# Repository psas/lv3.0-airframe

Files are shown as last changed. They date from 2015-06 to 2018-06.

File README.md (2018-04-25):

# PSAS Launch Vehicle 3 (LV3) 🚀

This is the repo for the LV3 airframe. This holds everything you need to know about making a rocket out of carbon fiber. This includes CAD files, design and prototyping logs, simulation and testing data, most of all the manufacturing procedures for the carbon fiber airframe modules.  

If you aren't allowed to push, send Joe or Andrew your Github username and ask for access. (This is different from getting added to the PSAS "organization".)

If you're looking to copy or build on this work check out the [doc directory](/doc/), especially the [layup procedure](/doc/mfg/moduleProcedure.md) and please message the people who have committed frequently/recently with any questions (or better yet, [make an issue with your question](https://github.com/psas/lv3.0-airframe/issues)).

If you want some quick physical specifications on the airframe, checkout the [quick facts.](doc/quickFacts.md)
For more detailed info, we have a [model](sim/ORK/LV3_L13.ork) for [OpenRocket](http://openrocket.info/) and a [model](cad/LV3.SLDASM) for [SolidWorks](http://www.solidworks.com/).

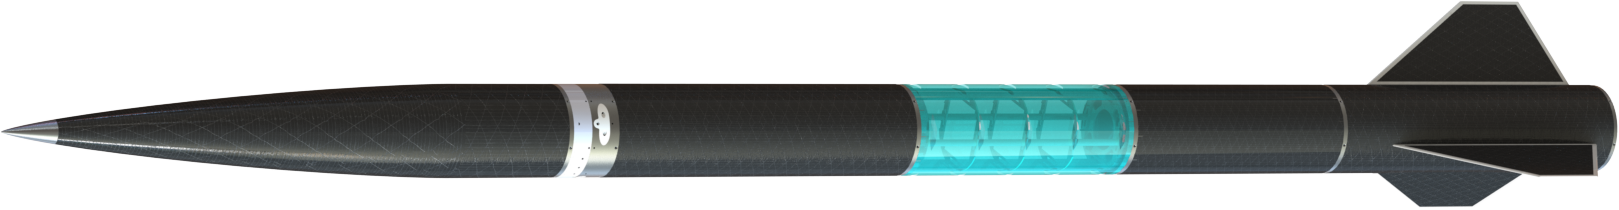
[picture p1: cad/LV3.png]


## Relevant Repositories
If you want to work on the CAD model, you'll need to have the dependencies cloned to the same directory as this repo. So, something like 

```
PSAS
├── lv3.0-airframe
├── lv3.0-recovery
├── lv3.0-camera-ring
├── lv3.0-umbilical-ring
├── sw-cad-airframe-nsr
└── reaction-control
```

You should also read the [Intro to Git workshop slides](https://drive.google.com/open?id=1pykfwvAw5q1oXGM8aLyhXPHOKDCI61YhK5w33QwzuFw) if you're new to Git
Also, read the [OreSat contributions guide](https://github.com/oresat/oresat-structure/blob/master/.github/CONTRIBUTING.md) if you're new to using SolidWorks with Git.

### Dependencies
* [psas/lv3.0-recovery](https://github.com/psas/lv3.0-recovery) -- CAD and analysis for the eNSR-based recovery system
* [psas/lv3.0-camera-ring](https://github.com/psas/lv3.0-camera-ring) -- 360 degree camera module based on the RunCam Split 2
* [psas/lv3.0-umbilical-ring](https://github.com/psas/lv3.0-umbilical-ring) -- passthrough module for the umbilical and arming switches (uses same format as camera ring)
* [psas/sw-cad-airframe-nsr](https://github.com/psas/sw-cad-airframe-nsr) -- Mechanical separation system for the nosecone/parachute
* [psas/reaction-control](https://github.com/psas/reaction-control) -- Cold gas reaction control system

### Historical
* [psas/LV3-design](https://github.com/psas/LV3-design) -- Early conceptual design of LV3
* [~~psas/mme-capstone~~](https://github.com/psas/mme-capstone) (**DEPRECATED**) -- One of the repositories created durring the 2014 capstone. This contains code for some of the tools they used. 
* [~~psas/sw-cad-carbon-fiber-process~~](https://github.com/psas/sw-cad-carbon-fiber-process) (**DEPRECATED**) -- Yet another repo from the 2014 team. This contains CAD for some of the tools they made.

## TODO:
[Check out the issues list if you're looking for something to do.](https://github.com/psas/lv3.0-airframe/issues) 
Keeping a TODO in the README never works out.

## Project Members
If you're working on the project in any way, please add yourself to this list.

IRL Name                       | Github username        | Current Role
------------------------------ | ---------------------- | ------------
Joe "Rocket Czar" Shields      | @Joedang               | project coordination; MFG; design
Leslie Elwood                  | @lelwood               | MFG; design; logistics
Alex "the Pretty Good" Farias  | @alexkazam             | MFG
Ian Zabel                      | @IanZabel              | cradle design; modelling
Kyle Blakeman                  | @kablakeman            | module sanding
Peter McCloud                  | @petermccloud          | CNC machining
Jorden Rolland                 | @JSRoland              | 
Katia                          | @kp07                  | 
Marie "Marie House" House      | @hmarie2               | anti-lithobreaking precautions
Adam Harris                    | @SaturnVF1             | MFG; manual machining
Josh Carlson                   | @paperman5             | CNC machining; design
Jacob Tiller                   | @JacobTiller           | machining; design
Erin Schmidt                   | @7deeptide             | system integration; design
Nathan Bergey                  | @natronics             | patron saint
Andrew Greenberg               | @andrewgreenberg       | benevolent dictator; pixie wrangler

## What and where
```
|-- cad						holds the Solidworks files for all the machined parts
│   ├── COTS					models for Commercial Off-The-Shelf parts
│   ├── CubeSatAirframeMount			"Cradle" that holds the flight computer (OreSat) inside LV3
|   |-- finCan
|	|-- LongFinFiles			current fin design (flyable and manufacturable)
|   |-- module					files for 18 and 24 inch modules
│   │   ├── jigs				jig for drilling side holes in module rings (and other radial parts)
│   │   └── layup
|   |-- nose					nosecone and mold subassemblies
|   |-- radome					radio-transparent fiberglass module
|   `-- railSled				part for interfacing with the launch rail
│       ├── CAM					G code for the rail sled (obsolete)
│       │   ├── Base
│       │   ├── Neck
│       │   └── Trunk
│       └── Old rail sled designs
|-- doc						all pure documentation
|   |-- aiaa-3.6.1				LaTeX template for AIAA
|   |-- extAbstract				extened abstract for the AIAA paper
|   |-- img					image resources for documentation
|   |-- mfg					step-by-step instructions for manufacturing
|   |-- paper					the conference paper we're submitting to AIAA Space
│   ├── FlightComputerMount			stuff about the Cradle
│   ├── textbook				summary of composite techniques in general
|   `-- updates					bi-monthlyish status updates on the project
|-- sim						simulations and calculations
|   |-- DATCOM					DATCOM cases for cross-validating the design (abandoned)
|   |   |-- case
|   |   |   |-- LV3				case for the LV3 airframe (not complete)
|   |   |   `-- exMiG
|   |   |-- doc					DATCOM documentation
|   |   `-- exlinux				example DATCOM cases
|   |-- ORK					open rocket models
|   |   `-- prev
|   |-- OpenFOAM				CFD models
|   |   `-- LV3\_LD-Haack			model of the 1:5 nose cone
|   |       `-- rcf_100				100-node-long mesh
|   |           |-- 0				initial conditions
|   |           |-- constant			fluid properites
|   |           `-- system			simulation parameters
|   |-- plots					plots of the open rocket data
|   |-- reductions				reductions of the openrocket simulations
|   `-- simData					output of the openrocket simulations
|-- test					data from physical tests on modules
|   `-- profilometer				surface roughness data
│   └── tinyMold				
└── tools					sources/CAD/docs for physical tools used to make LV3
    ├── Composite_Table				the table we do all the layups on
    ├── crusher-control				controller software for one of the crush testers at PSU	
    ├── oven-controller				the temperature controller for the oven
    │   ├── Oven_Controller			the temperature controller for... wait
    │   │   ├── Box				enclosure for the oven controller
    │   │   ├── OvenControl			the temperature contr-- again?!
    │   │   └── oven-controller-master		"A Deja Vu is usually a glitch in the Matrix."
    │   └── src					source code for the controller
    ├── Sheet_Cutting_Templates			templates used to cut sheets of CF, adhesive, et cetera
    └── strain-gauge-amplifier			instrument used to take strain measurements in a crush/tensile test
```

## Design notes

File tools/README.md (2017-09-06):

# General Tools for Making the LV3 Airframe
This directory only contains general tools. 
To a large extent, the designs found here would be useful for *any* composites work. 
Many stages of the airframe manufacturing process require specialized tools that are only applicable to one part of the airframe.
You will find those designs along side the CAD files for their respective parts in the [cad/](../cad/) directory.

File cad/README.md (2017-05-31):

lv3.0-airframe/cad/
=====================

# Solid Works CAD for the LV3 launch vehicle

## Dependencies:  
psas/sw-cad-airframe-nsr	
psas/reaction-control	

See:   https://github.com/psas/sw-cad-common#psas-solidworks-setup-and-use-procedures for procedures on using github for Solidworks files

### Heads up:  
SolidWorks still doesn't support building assemblies with relative file paths for some reason. If you are working on an assembly after someone else, you will have to show SW where the referenced parts are. 

## TODO: 
* Create tip-to-tip shells
	* Add TTT shells to the assembly
* Incorporate eNSR guts into main assembly
* Incorporate flight computer cradle assembly into main assembly
* Incorporate recovery system assembly into main assembly
* Incorporate RCS guts into main assembly
* Figure out how to keep SW from always modifying the parts in an assembly! (makes it hard to tell what's really changed)

## Technical Drawings
All of these `PDF`s should correspond to a `SLDDRW` in the same directory.  
_To rebuild this list, run the `listpdf.sh` script in this directory._

[./couplingExample.pdf](./couplingExample.pdf)  
[./railSled/sledJig.pdf](./railSled/sledJig.pdf)  
[./nose/jenkyNoseTip.pdf](./nose/jenkyNoseTip.pdf)  
[./nose/noseplug.pdf](./nose/noseplug.pdf)  
[./nose/dummyNoseTip.pdf](./nose/dummyNoseTip.pdf)  
[./nose/nosePlug2.pdf](./nose/nosePlug2.pdf)  
[./nose/von_karmon_nose_tip2.pdf](./nose/von_karmon_nose_tip2.pdf)  
[./module/maleRing.pdf](./module/maleRing.pdf)  
[./module/layup/mandrel24.pdf](./module/layup/mandrel24.pdf)  
[./module/layup/dummies.pdf](./module/layup/dummies.pdf)  
[./module/femaleRing.pdf](./module/femaleRing.pdf)  
[./finCan/fin_jig_top_bottom2_TechDrawing.pdf](./finCan/fin_jig_top_bottom2_TechDrawing.pdf)  
[./finCan/fin_jig_mid_TechDrawing.pdf](./finCan/fin_jig_mid_TechDrawing.pdf)  
[./finCan/LongFinFiles/LongFins_ALedge.PDF](./finCan/LongFinFiles/LongFins_ALedge.PDF)  
[./finCan/motorMount.pdf](./finCan/motorMount.pdf)  
[./finCan/finLayup_jig_baseplate.pdf](./finCan/finLayup_jig_baseplate.pdf)  
[./finCan/spider.pdf](./finCan/spider.pdf)

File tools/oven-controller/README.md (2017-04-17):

oven-controller
===============
This is kind of a dumpster fire. It was clearly its own repo at some point and somebody downloaded the ZIP for that repo and just plopped it here. There's a completely different version of the software as made by the 2014 capstone team versus the CS student. The CS version uses deprecated Arduino libraries and focuses *way* more on making a fancy GUI than a functional tool. 

We don't even have this oven at PSU anymore. We replaced it with a commercial oven for legal reasons. My advice: _**if you want to build a temperature controlled oven, just buy a commercial controller!**_ 
You can get constant-temp controllers off of Amazon for 20 to 30 USD and ramping/soaking controllers (exactly what you need!) off of ebay for like 80 USD.

For the composites oven team at Portland State. 

v0 - the original schematic representation of the current working breadboard setup.

v1 - the finished Arduino shield version on a printed circuit board. this works! 

v2 - additions to the v1 Arduino shield design.

v3 - developing final version for OSHPark order.

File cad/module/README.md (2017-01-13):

# module/
This folder contains the parts and assemblies for the generic LV3 modules.

### carbonSleeve24.SDLPRT
There's a graphical glitch -- at least on my machine -- that makes the rings show through the carbon fiber. They are in fact smaller.

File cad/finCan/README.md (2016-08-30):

The fin can is waiting to have the new fins added in and the whole thing reassembled. 
The CAD files for the fin jig are fin_jig_mid and fin_jig_top_bottom2. The jig keeps the fins aligned as you adhere them to the surface of the rocket module.

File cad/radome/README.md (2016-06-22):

Currently, these files describe the old radome section designed by the 2014 team. 
The new plan for the LV3 radome is to make an 18" module of fiberglass. 
So, these designs are obsolete.

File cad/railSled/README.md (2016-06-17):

This is the part that holds the rocket onto the rail during launch. 
It's meant to adhere to the side of the fin can.
We currently don't have much of a plan to align it.
The CAD and CAM are done. 
The first try at machining the aluminum base didn't turn out well...
If you're coming back and looking at the CAD files, don't judge too harshly. This was one of the first real parts I made in Solidworks.

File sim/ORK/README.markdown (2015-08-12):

# Airframe Simulation

File for simulating the LV3 class airframes

## OpenRocket Files:

 - `LV3.0_L.ork` Using a small L class motor
 - `LV3.0_N.ork` Using our standard 6 grain 98mm case
 - `LV3.0_O.ork` Using a huge motor

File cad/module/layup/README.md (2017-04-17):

lv3.0-airframe/cad/module/layup
=========

This contains CAD for parts required for a module layup. It was imported from an old repo from 2014 and most of the files have been renamed to conform to the style of the rest of this repo. So, you will probably have to relink the assemblies when you open them.

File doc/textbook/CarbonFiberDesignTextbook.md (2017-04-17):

### 

### Abstract:

The purpose of this manual is to provide a space for documentation of knowledge and research necessary to the Composite Airframe Capstone Team. It will serve as a running manual for sharing information between team members, and as a textbook style resource for future airframe designers on PSAS to use for future iterations. Information for this book was taken from various texts, videos and conversations with industry professionals. It is supposed to be a concentration of data from available sources.

Bibliography:
=============

Fiberglass and Other Composite Materials- A guide to high performance non metallic materials for race cars, street rods, body shops, boats and aircraft. HP books. Forbes Aird

Introduction to Composite Materials Design. Ever J Barbero, department of mechanical and aerospace engineering, West Virginia University, USA. Taylor and Francis group

Taylor, Travis. *Introduction to Rocket Science and Engineering*. CRC Press 2009. Boca Raton, FL.

Composite Airframe Structures, Michael Chun-Yung Niu. 978-9627128113. Hong Kong Conmilit Press Ltd.

Aramid (Kevlar) Fiber
---------------------

DuPont’s aramid product is called kevlar. A high modulus version called kevlar 49 is widely used for composites. Kevlar 149 has higher stiffness but less strength, and Kevlar 29 is not very stiff but is used in body armor.The compression strength of a Kevlar laminate, however, is limited by the apparent inability of any resin matrix to wet the fine fibrils that make up the fiber bundle; the outside of the bundle gets surrounded by the resin and attached to it, but individual fibrils do not. As a result, when a laminate is loaded in compression, the individual fibrils buckle when the stress exceeds about one fifth of what it would take in tension. Thus, the properties of the laminate become dominated by the characteristics of the resin matrix, and a Kevlar laminate’s strength in compression is limited to relatively low values.

On the other hand, the gradual buckling of the fibers acting under the restraint of the matrix means that an aramid laminate does not fail in a brittle manner like those made from other structural fibers, but “yields” much like metals. In the process of failing in this way, a substantial amount of energy gets absorbed, which makes it attractive to manufacturers of aircraft and race cars. This property together with its all around toughness (which is why kevlar is very difficult to cut cleanly) also makes it very popular for lightweight canoes and kayaks.

Kevlar can be used by itself or in combination with other fibers. Either as one or more separate plies, or woven together into a hybrid fabric. Combined in these ways with CF, it is widely applied in race car construction as a hedge against the brittleness of carbon. You won’t see much crumpled carbon fiber in crashes- it just explodes into dust when it is grossly overloaded in this way.

Another significant feature of kevlar is its light weight. An aramid based laminate will typically wind up about 20% lighter than a part of the same thickness using glass or, for that matter, carbon. Used as a direct substitute for glass reinforcement in lightly stressed body panels, kevlar cloth yields a part that is about ⅕ lighter yet stronger than the part it replaces. Kevlar deteriorates slowly when exposed to ultraviolet light, so some sort of paint or other covering is needed to exclude UV from a kevlar laminate. This hardly matters in practice because Kevlar is invariably combined with epoxy resin, which itself needs protection from UV, no matter what the reinforcement.

Composites made from Kevlar 49 compare unfavorably to carbon fiber composites in terms of stiffness, both on a per volume and a per weight basis. On a same weight basis, a Kevlar 49 laminate will give one half to one quarter the stiffness of one made from carbon.

Fabrics
-------

There are tons of different kinds of fabrics. Unidirectional fabric has most of the fibers running one way, with just a light crossweave at wide intervals to hold the whole thing together. This means all of its strength is in one direction. Others have an equal number of yarns running in both the lengthwise (called the warp), and the crosswise direction (the fill), producing a balanced, bi-directional fabric with equal strength properties in both the lengthwise and crosswise directions. Of course strength and stiffness are degraded heavily when you rotate the carbon between 0 and 90 degrees.

Weaves
------

For any basic type of weave, the strength and stiffness of the finished product depends on the volume fraction of fiber. Tight weaves give the best strength and stiffness values, but are more difficult to wet out; open weaves are easier to saturate, but yield a laminate which is less strong because of the greater proportion of weak plastic in relation to the amount of strong reinforcement.

Satin Weave
-----------

Crimping of the yarns is reduced if each warp yarn crosses over more than one fill yarn before crossing under one. Such patterns are generally termed satin weaves, and are further identified by the number of successive fill threads that are skipped over; thus there are five-harness and seven-harness satins etc. Because of this more advantageous geometry, laminates using satin weave fabrics generally show slightly superior strengths than those made from square weave materials, especially when loaded in compression. Because the yarns in a satin weave can skew more easily than in a square weave, they have superior drapeability, it is easier to get them to conform to tight curves, especially ones with complex changes in radius. Also, satins yield a smoother surface finish than a square weave of the same height. Taken together, these advantages often justifyn the slightly higher cost of satin weave fabrics.

Polyester
---------

Although other resin systems are starting to make inroads, especially for high performance applications, the overwhelming majority of FRP work (&gt;90%) is based on polyester. Epoxies usually produce stronger laminates than polyester. the surface of kevlar just doesn’t seem to connect well with polyester.

Beyond the fact that they are cheaper than epoxies by half or more, polyesters remain predominant for the very good reason that they are easy to work with. First, they are low in viscosity, which means it is easier to pour pump mix etc. The cure rate of polyester can be adjusted over a wide range varying the amount of catalyst added, which is absolutely not the case with epoxy. Finally, polyester is arguably less hazardous to work with than epoxy, though it might be better to say that the hazard is different.

Polyester has several drawbacks, however. It is generally inferior in strength to laminates done with epoxy…

These are the cheapest of all the resins. They have poor bonding capability and should never be used for any structural carbon or aramid work. They typically work well only on fiberglass. One should generally never consider using this resin with structural applications with Carbon Fiber or Aramid.

**Styrene-Suppressed Resins**

If you have read or heard anything about FRP work, you will probably have encounter a distinction made between laminating resin and surfacing resin. A feature of conventional polyester blends is that their cure is inhibited by exposure to oxygen in the atmosphere. What that means is that while the bulk of the resin will cure soid, a very thin layer on the top surface will remain tacky. This helps subsequent layers to bond to one another, so this laminating resin is used wherever additional plies are to be added.

Epoxy
-----

Laminates using epoxy generally have greater strength and better chemical resistance than those using polyester, especially at higher temperatures. Epoxy also shrinks less than polyester (40 to 50% less) depending on the curing agent used. As well, some fibers like kevlar and carbon are incompatible with polyester. On the other hand, epoxies are distinctly trickier to handle than polyester, introduce different health risks, and both they and their curing agents are significantly more expensive.

Epoxy resins used in composite fabrication are more viscous and sticky than polyesters. This makes it more difficult both to ensure complete mixing of the resin and hardener, and to wet out the reinforcement, adding to labor and increasing the risk of areas of incompletely saturated resin reinforcement. It is worth emphasizing here that the neccessity for complete and thorough mixing of epoxies. To ensure that all of the resin is mixed with all of the hardener, suppliers urge that you change containers during the mixing. Here’s how: dispense resin into A, and mix thoroughly, scraping the side of the container to deal with either component that may be sticking to the sides. Then pour this mixture into cup B, and continue to mix. Any unmixed resin or hardener remaining in cup A will have been left behind. If you are proportioning the two components by weight, rather than by using a proportioning pump, then you may even have to resort to a three cup technique. This sounds a bit obsessive, but there is little doubt that most problems with epoxy result either from an incorrect resin to hardener ratio, or from inadequate mixing.

Thinners are available to reduce the viscosity of epoxy resins. Although these are reactive with dilutents, they cross link with the resin in much the same way that styrene does with polyester, they should be employed with caution. Dilutents may reduce the strength and chemical resistance of the finished product, and certainly will if added in sufficient quantity to make the resin as easily worked as polyester. Some thinners are particularly toxic.

Mixing is the second problem with epoxies. Epoxies must be mixed with the resin in a specific proportion, and some require very accurate measurement. If off by more than a smidgen the result can be anything from an incomplete cure, to no cure at all. What’s more, this intolerance of variability in the hardener to resin ratio makes it so the cure rate of epoxy systems cannot be adjusted by varying the amount of hardener. If you want to speed up the cure, you have to pick a different curing agent, or increase the temperature of mold/workspace.

The very strongest laminate produced with epoxy systems have to have an elevated curing temperature usually from 100F to 350F.

Carbon Fiber parts will absorb radar microwaves.

Note that most epoxies are slightly amber in color. When you apply the typical amount of resin to a composite, that is just enough to wet-out the composite, the epoxy is clear.

There are only about 4 epoxies in the market that will not yellow over time. The West System 207 is the best of them all (that is the reason we sell West System's Epoxy). Even for indoor applications, UV will eventually yellow your epoxy. So if you don't plan on painting you piece/application and you want your piece to look good and last as long as possible, plan either protecting it with UV coating (such as a UV urethane), and/or use the 207 hardener.

Gel Coat
--------

To produce parts with a smooth shiny surface comparable to painted metal, something needs to be done about the appearance of raw fiberglass mat, or the fabric weave of cloth. For such parts, a coating of pure plastic resin containing no class or other fiber is usually applied to the mold surface and permitted to cure before any glass is applied. Conventional gel coat is nothing more than polyester resin, with a few added ingredients. To prevent runs and sags when the gel coat is applied to a vertical surface, a thixotropic agent, usually silica gel, is blended in, to add body and so resist the flowing under the effect of gravity.

MEKP
----

MEKP is a clear colorless liquid. It is explosively unstable in its pure form and so is supplied as a diluted solution in an inert liquid buffer. While it is not itself highly flammable, it is a powerful oxidizer which may cause some readily flammable substances- like paper, rags, or sawdust- to ignite spontaneously if it comes in contact with them. It is also quite corrosive, and prolonged contact will cause skin burns. Splashed in the eyes can cause permanent damage. The vapors may cause headaches and intoxication, and corrosive damage to the nose, throat and lungs. This is the catalyst for polyester resins.

PVA
---

With a new mold, you first wax and thoroughly buff several times, at least three. (You don’t need that much wax, but you might have missed a few spots the first time. Terry-cloth toweling seems to work well for the waxing and buffing. Next, you apply a coat of polyvinyl alcohol, which dries to form a thin barrier film that provides a second line of defence against the nightmare of a part firmly stuck in the mold. PVA is not only unnecessary in a well made, aged mold, it is undesirable since the PVA leaves a slightly pebbly, orange peel texture on the surface of the finished part that has to be polished out.

It is possible to apply without a spray gun (a small piece of old t-shirt seems to work better as an applicator than a brush), but spraying is definitely preferable. The PVA should be sprayed in stages, starting with a very light misting, and finishing with several heavier coats. Obtaining a uniform and, above all, a continuous film of PVA is much easier if the mold has a color that contrasts well with the PVA, which is green.

Elevated Temperature Curing Epoxies
-----------------------------------

For applications where minimum weight and maximum strength are important, higher performance resins may be selected, and that often means epoxy resin systems designed to cure at higher than room temperatures. For a true high temperature cure (HTC), the temperatures required with some resin systems are so high (up to 400F) and the demand for close control of the heating so strict that homemade arrangements are inadequate. The only solution is a purpose-built oven, fitted with precision timers and automatic temperature controls. Large and expensive industrial ovens are available for this purpose.

Heating Methods
---------------

Never forget that an oven is simply an insulated box with a heat source inside; in some cases it may be quite practical to make your own. It is not prohibitively expensive to construct a frame for a simple shed-like structure out of steel (not wood), with sheetrock walls and ceiling, heavily insulated on the back side with rock wool or fiberglass batts (forget about foam insulation; apart from increased fire risk, insulating foams may soften at the temperatures involved).

Cautions- while undiluted epoxies do not include flammable, low boiling point solvents, like the styrene in polyester and vinylester resins, these materials are nevertheless flammable, and extreme care must be taken to avoid fire. That pretty much limits the possible heat sources to electricity, steam and hot water, through the use of water is obviously limited to temperatures below its boiling point of 212F.

Heating the mold is another alternative to heating the air. Possible to use electric resistance heaters.

Expansion
---------

Another factor to bear in mind whenever exposing a laminate and mold assembly to elevated temperatures is the issue of compatibility of the mold and laminate materials. For one thing, their comparative thermal expansion has to be considered, especially if the dimensions of the part are critical. For example, some carbon fibers exhibit negative thermal expansion- they get smaller as they heat up. Other forms of carbon fiber do have a positive thermal expansion coefficient, but they grow much less with heat than most other FRP materials. For this reason, the molds for carbon fiber reinforced race car and aircraft components using ETC resin systems are themselves usually made from the same CF as the part, to ensure that the mold and laminate shrink and grow in sync.

Fabric impregnator
------------------

There is also a method of working that involves something like a homemade prepreg, using a machine called a fabric impregnator. This apparatus mechanically draws woven or unidirectional goods through a bath of resin and then passes it through a set of pinch rollers, yielding more uniform resin distribution and a higher reinforcement to resin ratio than is usually possible with hand work. At the same time, labor is reduced.Virtually any liquid resin system can be used in this process., for unless the material is going to be used almost immediately it is obviously an advantage if the resin either cures very slowly at room temperature or can have its cure postponed in some way. Epoxy based systems which can be arrested at the b-stage are well suited to this technique, and this, in fact, is the way commercial prepregs are made. There is also the possibility of using UV curing polyester or vinylester resins. If the dipping were done under a “safe” light, the impregnated fabric could be rewound onto a roll, using a sheet of polythylene to prevent layers from sticking together, and would store indefinitely until exposed to UV light, such as by being taken outdoors. The cost of fabric impregnating equipment generally limits its use to those who either need large quantities of material or are working with weight and strength critical goods, or both. Prepregs can also be produced by a filament winder.

Male or Female?
---------------

Assuming conventional hand layup, the surface of the finished product that contacts the mold will have a glossy surface, while the back face will be rough, so for goods where visual appearance is important, the surface that is exposed determines which way it must be molded. Thus, a bathtub would be formed over a male mold, while a canoe would be made in a female mold.

The Expendable or Sacrificial Mold

One is a technique for making tanks of all sorts by carving a chunk of foam to the desired shape, wrapping it entirely with resin saturated reinforcement, and then dissolving out the foam plug with a suitable solvent once the shell has cured. This is undeniably an intriguing technique, but there are a few intrinsic limitations: the foam must be unaffected by the resin system; the resin must be impervious to the solvent used to purge the core; the thickness of the wrapping may need to be taken into account when shaping the core; and the outer surfaces of the finished tank necessarily has the texture of the fabric used.

Fatigue
-------

An advantage of composite materials sometimes touted in print is that they do not fatigue. This is simply not so, though it is true to say that the fatigue resistance of composites is generally superior to that of metals. Unidirectional laminates using kevlar retain about ¾ of their static strength after ten million cycles of loading in tension (though they do less well when the loading reverses between compression and tension); similar carbon fiber laminates keep perhaps two thirds of their original strength; glass fiber composites are down to about half by that point.

**Sandwich Structures**

Sandwich structures present particular problems around bolted connections, and anyplace else where loads are highly localized. One technique for dealing with this is to remove the core in the area surrounding the attachment, and bring the two skins together, locally reinforced with additional layers of laminate. It is common for at least some of this extra material to be a thin sheet of aluminum, to take advantage of its isotropic, ductile nature.

Surface Bonding
---------------

Provided the surface is properly prepared, aluminum will bond securely to an epoxy laminate. The key phrase is properly prepared. Understand first that aluminum oxidizes- exposed to air, the bare surface of a piece of aluminum almost instantly reacts with the oxygen in the atmosphere to form aluminum oxide. If you attempt to stick anything to an untreated piece of aluminum, what you wind up doing is gluing to the oxide, not the aluminum itself. In principle, that ought not to be a problem, provided, first, that the oxide is well and truly attached to the metal beneath and, second, that the adhesive is well and truly bonded to the oxide. There are potential problems on both scores, as the aerospace industry discovered when they began gluing airplanes together.

To cut a very long story short, the procedures that Boeing and the other heavy hitters involve a succession of steps to de-grease, acid etch, and anodize with phosphoric acid, with rinsing in deionized water after each step.

**How FRP Composites Carry Loads**

Many people believe that the strength of an frp laminate is unnecessarily reduced whenever any of the fibers in it are broken. This is definitely not so. It is equally untrue that a fiber has to extend from one end of a load carrying part to the other in order to contribute to the strength of the laminate.

First realize that a fiber, by definition, is something that is many times longer than its diameter. Now, in a properly constructed laminate, all of the surface of each fiber is firmly attached to the resin that surrounds it, and the area of that contact is many times greater than the cross sectional area of the fiber. Now imagine a small zone within the laminate where two fibers, lay side by side, fairly close to each other, but only partly overlapped in strength, so one is closer to one end of the laminate, overall, and the other closer to the opposite end.

If we anchor one end of the laminate and pull on the other, there will be a tendency for the two fibers to slide past each other. Each, however, is stuck to the surrounding resin, so the interface between fiber and resin is stressed in shear- the fiber is trying to slide through the resin, and the “hands off” the load to the next adjacent fiber. Provided each fiber is long enough in relation to its diameter, then even though the shear strength of the resin is a mere fraction of the tensile strength of the fiber, there will be so much more resin carrying the shear load than there is fiber carrying the tension load that the the fiber will break before the plastic does.

There is some minimum length of fiber for which this will be true, and that is why a laminate made with say, short chopped strand reinforcement will not be as strong as one using longer fibers. On the other hand, if the minimum length criterion is met, longer fibers will not make the laminate any stronger. Equally any more resin than is needed to pass the load from one fiber to the next does nothing to increase the strength of the laminate and just adds weight.
Another way to look at it is on the basis of tensile stresses. In the previous chapter, we saw that any material which is pulled lengthwise will stretch somewhat, or strain, and that amount of this strain depends on just two things- the stress and the elastic modulus. Now when a composite is stress, all of it grows longer- the fibers and the resin have equal strains. The fiber, however is many times stiffer than the resin, so assuming that half the volume of the composite is fiber and half is resin (a representative figure), then the stresses in the two will be in the same ratio as their elastic moduli- about 25 to 1! Clearly, the matrix is lightly stressed, even when the fibers are carrying a very large load, and since the area of contact between the fiber and the plastic extends over the whole surface of the fiber, the matrix has no problem transmitting the load from one fiber to another.

Wet Lay-up
----------

When honeycomb core is used in wet lay-ups, it is common to first produce one skin, then for the core to be set down on the still wet laminate, so the laminating resin serves as the adhesive for this connection. The second skin is more problematic. If a wet lay-up is applied over the core to produce the second skin, there will be a tendency for the resin to drain out of the reinforcement and into the cells. About the only practical alternative is to produce the second skin independently, then to assemble it to the core using a film type adhesive. This obviously demands closer than typical control over the shape and dimensions of both core and skins.

Pre-Preg
--------

When the facings are produced from prepregs, this problem is avoided, and the choice is then between production of the two skins, allowing them to fully cure, followed by assembly to the core using film adhesive, or by letting the resin in the prepreg serve as the glue and completing the assembly before either skin is cured, a technique called co-curing. Notably, the force required to peel the skin away from the core is different for the upper surface than from the under surface. This occurs because the differences in the shape and size of the fillet of resin that forms and the junction between each cell and the skin, in turn cause by the flow of the resin under gravity during the cure.

Fiber volume fraction
---------------------

The volume of fiber in a cured composite. The fiber volume of a composite material may be determined by chemical matrix digestion, in which the matrix is dissolved and the fibers weighed and calculated from substituent weights and densities or a photomicrographic technique may be used in which the number of fibers in a given area of a polished cross section is counted and the volume fraction determined as the area fraction of each constituent. Typical values for boron/epoxy and for graphite/epoxy, based upon the fiber type, is 55-67% fiber.

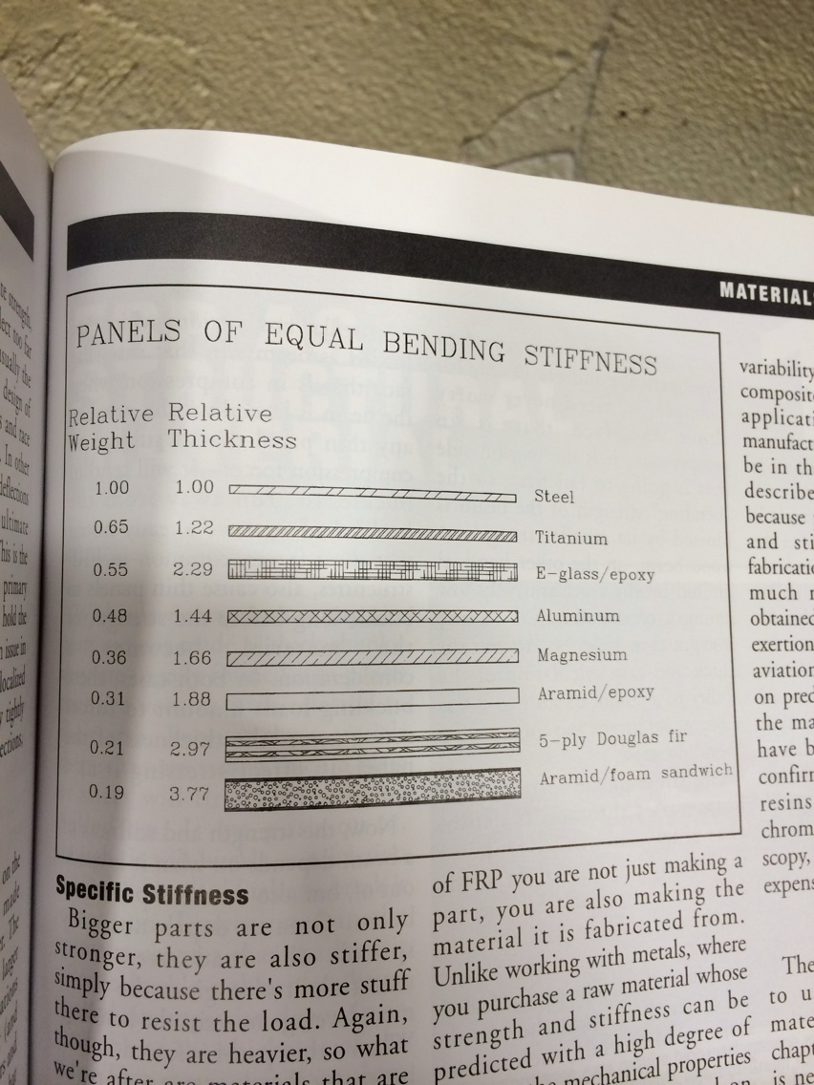
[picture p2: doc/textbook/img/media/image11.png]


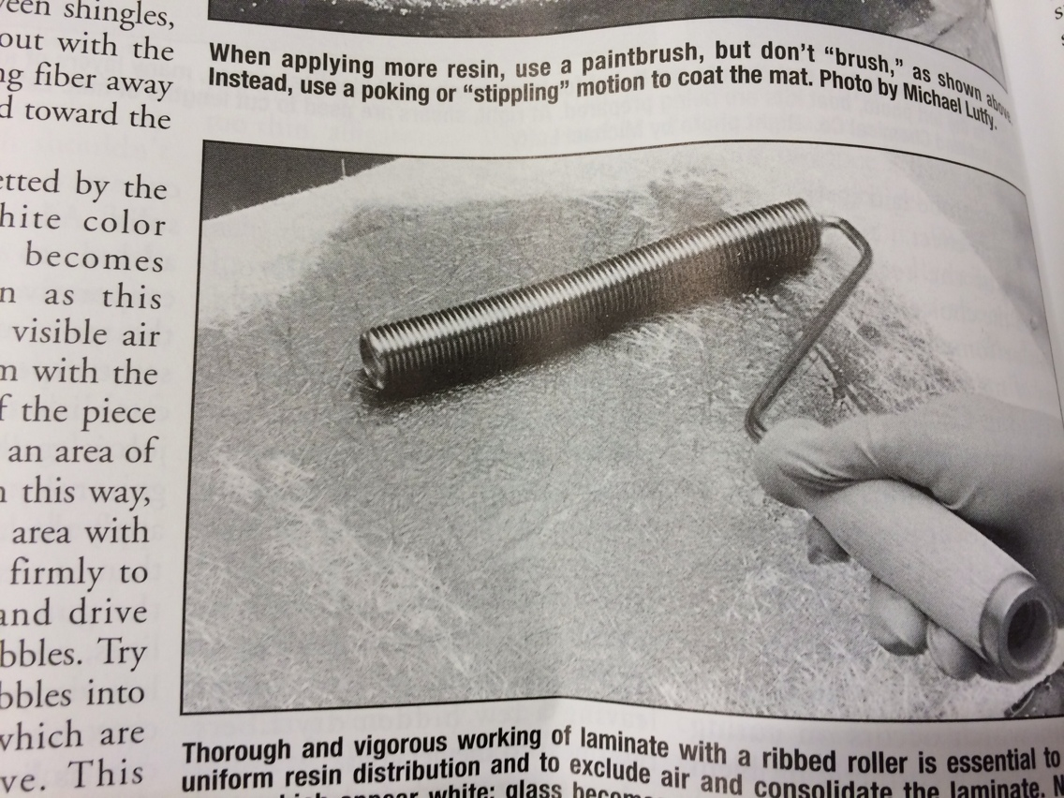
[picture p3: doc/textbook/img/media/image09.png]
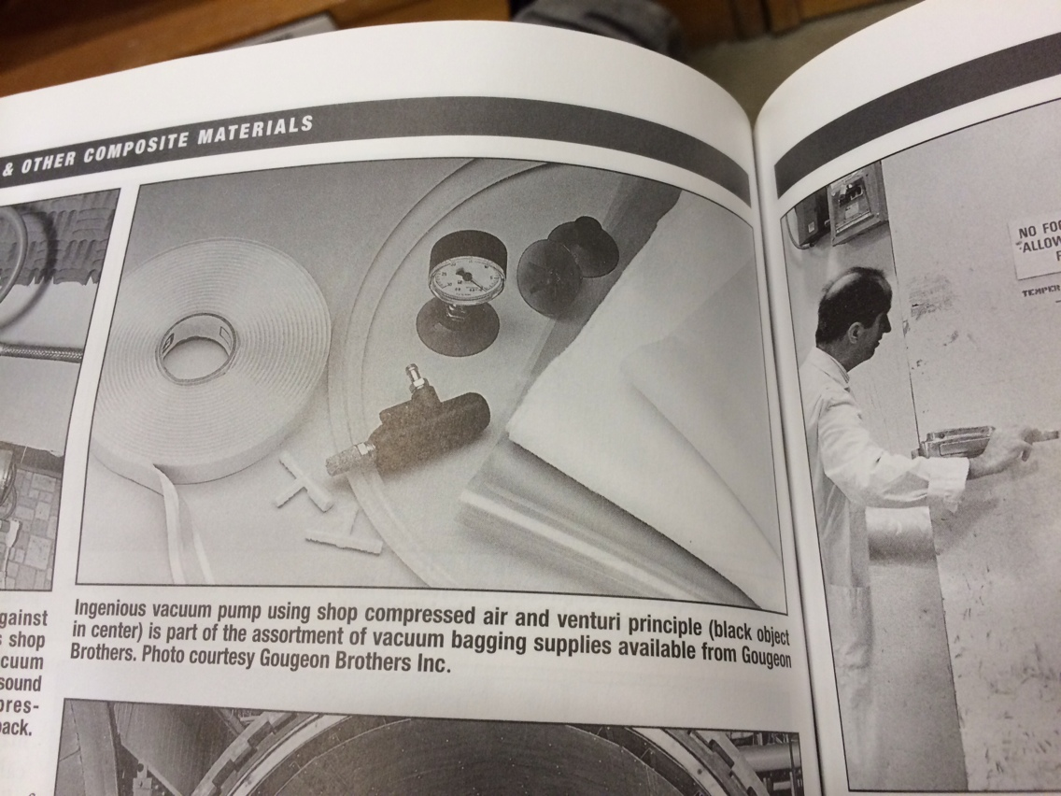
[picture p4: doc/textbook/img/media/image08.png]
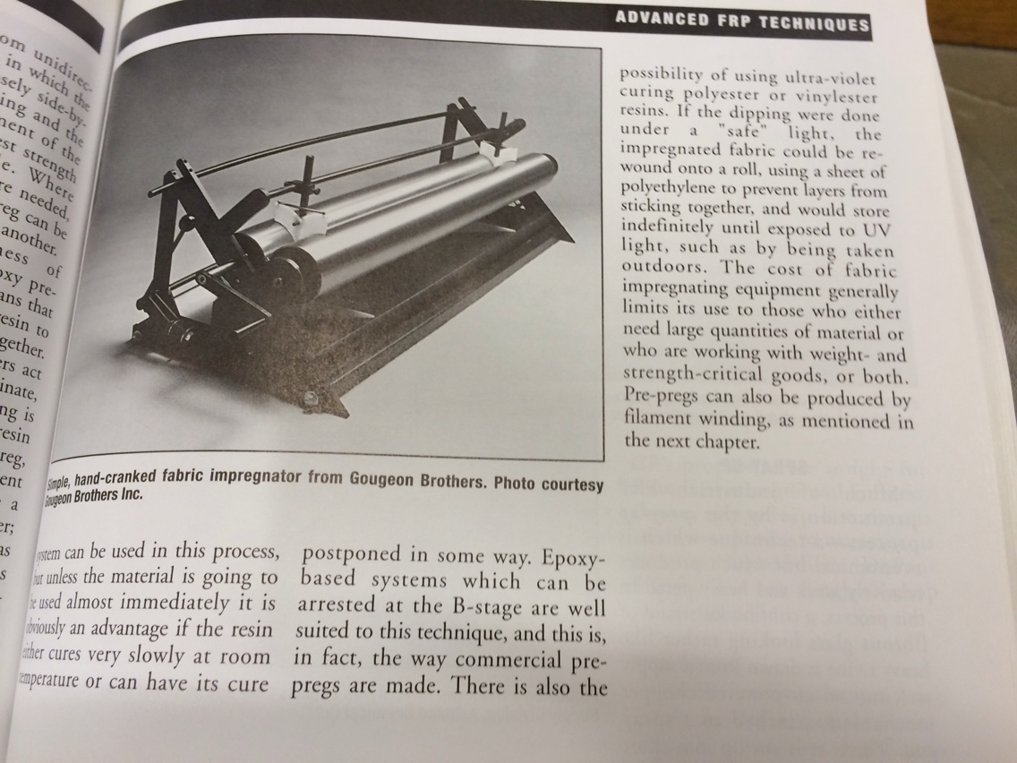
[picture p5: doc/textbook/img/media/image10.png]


Mat, fabric and veil
--------------------

A mat is formed by randomly oriented chopped filaments, short fibers, or swirled filaments loosely held together with a very small amount of adhesive. A veil is a thin matt used as a surfacing layer to improve corrosion resistance of the composite. Veils and mats have fibers oriented randomly in every direction, leading to isotropic properties in the composite. Nonwoven fabrics are made directly from strands without the intermediate twisting of the strand into yarns.

Epoxy Resins
------------

Epoxies shrink less than other materials (1-4% by volume) which helps explain their excellent bond characteristics when used as adhesives. Epoxies are less affected by water and heat than other polymer matrices. Epoxy resins are also favored for their simple cure process that can be achieved at any temperature between 5C and 150C.

Isotropic/Anisotropic
---------------------

Isotropic materials (aluminum, steel) have the same mechanical properties in any direction. A typical example is the modulus of elasticity of wood, which is higher along the length of the tree and lower across the growth rings. The stiffness of an isotropic material is completely described by two properties, for example, the modulus of elasticity E and poisson’s ratio V. In contrast, up to 21 properties may be required to describe anisotropic materials.

Micromechanics and Fiber volume
-------------------------------

The stiffness of the equivalent CFRP material can be represented by five elastic properties:

E1: modulus of elasticity in the fiber direciton

E2: modulus of elasticity in the direction transverse to the fibers

G12: inplane shear modulus

G23: out of plane shear modulus

v12: inplane Poisson’s ratio

All of these are functions of the fiber volume fraction

These are of a similar naming scheme to how solidworks and ABAQUS call their variables

Thermal Expansion
-----------------

The thermal expansion coefficient of all resins are positive (about 30 to 100 E-6 /C) which is higher than steel alloys. Carbon fibers have a negative expansion in the fiber direction (-.99 E-6/C) and a relatively large expansion in the transverse direction (16.7 E-6/C). This means that depending on the amount of fibers (fiber volume fraction) it is possible to tailor the coefficient of thermal expansion of the composite to the user’s needs. Especially, it is possible to produce a composite material with a very low coefficient of thermal expansion, which is useful when dimensional stability is required.

Symmetric laminates experience no bending extension coupling. This is very important during fabrication because curing and subsequent cooling of the composite induces thermal forces. If the laminate is not symmetric, these forces will induce warping of the final part.

Longitudinal Tensile Strength
-----------------------------

The simplest model for tensile strength of a continuous composite is derived by assuming that all the fibers have the same tensile strength. Actually the tensile strength of fibers is not uniform. Instead, it is well approximated by a Weibull distribution. But as a first approximation it is assumed that all the fibers have the same strength equal to the average strength.

The second assumption is that both the fibers and the matrix behave linearly up to failure. This is not true for most polymer matrices that exhibit either elastic nonlinear or plastic behavior after a certain elongation. The behavior of polymers is further complicated by their load-rate dependency. That is, polymers are viscoelastic or viscoplastic.

The third assumption is that the fibers are brittle with respect to the matrix. Such large elongations to failure for fibers hold only in ideal conditions, with some fibers breaking at much lesser strain levels.

The fourth assumption is that the fibers are stiffer than the matrix. This is valid.

Under the assumptions listed, the composite will usually break when the stress in the fibers reaches their strength (average strength). After the fibers break, the matrix is unable to carry the load. Therefore, the composite elongation to failure, is equal to the fiber elongation to failure. At this strain level, the matrix has not failed yet because it is more compliant and can sustain larger strains. Under these conditions, it can be assumed that the longitudinal tensile strength is controlled by the fiber strength. This assumes the strain in the matrix and the fibers are the same, which is true if the fiber-matrix bond is perfect. The ultimate strain or stress of the matrix is not realized, because the fibers are more brittle.

Longitudinal Compressive Strength
---------------------------------

Compressive strength of continuous composites is lower than the tensile strength, about one half or less. The mode of failure is usually triggered by fiber microbuckling, when individual fibers buckle inside the matrix. The buckling process is controlled by fiber misalignment, shear modulus, and shear strength of the composite.

Fiber misalignment measures the waviness of the fibers in the composite. Fiber waviness is always present to some extent, even when great care is taken to align the fibers during processing. Waviness occurs because of several factors. The fibers are wound in spools as soon as they are produced, which induces a nature curvature in the fibers. Then fibers tend to curl when stretched on a flat mold. Furthermore, many fibers are wound together over a spool to form a tow or roving during fiber production. The fibers wound on the outside of the spool are longer than those wound in the inside. When the tow is stretched, the longer fibers are loose and microcatenary is formed.

Microcatenary can be shown by stretching a tow horizontally and letting the longer fibers hang under their own weight. The longer fibers hang in a catenary shape, just as electrical power lines do. In the final composite part, microcatenary appears as fiber misalignment.

The first formula for compressive strength was proposed recognizing the fact that compression failure is triggered by fiber microbuckling. The first approximation to the problem is to assume that the buckling load of the fibers is the limiting factor for compressive strength. To obtain the buckling load, some guy performed a stability analysis of straight fibers laterally supported by the matrix. Furthermore, the shear stress-strain law of the composite was assumed to be linear. Actually, PMCs have a nonlinear stress-strain law, as shown below. Such behavior is better represented by the relationship 4.66: tao= F6 tanh(g12 gamma /F6)

This approach can be used with an empirical correction, with testing for compressive strength.

Dimensionless compressive strength can be modeled in terms of dimensionless numbers, with the following formula 4.75: F1c=(X/a+1)^b G12. On page 94 from Intro to Composite materials design.

Laminate Description
--------------------

The notation used to describe laminates has its roots in the description used to specify the lay-up sequence for hand layup using prepreg. When using prepreg, all layers have the same thickness and only the angles need to be specified. In the hand layup process the laminate is built starting from the tool surface, or bottom of the laminate, adding layers on top. Therefore, the layers are numbered starting at the bottom and the angles are given from the bottom up. For example, a two-layer laminate may be \[30/-30\], a three layer one \[-45/45/0\] etc.

If the laminate is symmetric, like \[30/0/0/30\], an abbreviated notation is used where only half of the stacking sequence is given and a subscript ‘s’ is added to specify symmetric. The last example becomes \[30/0\]s. Since most laminates used are symmetric, there is the possibility of confusion when no subscript is used. To eliminate the possibility of confusion, a subscript ‘t’ may be used to indicate that the given is the total for example \[90/0\]T. A subscript number may be used to indicate a repeating pattern. For example \[(90/0)2\]T.

If the thicknesses are different use a subscript next to the degree marker. For example \[90t1/90t2/0t1/0t1\]S would mean a layer of the first thickness at 90, a layer of the second thickness at 90 etc. If all layers have the same thickness, the laminate is called regular.

Symmetric laminates experience no bending extension coupling. This is very important during fabrication because curing and subsequent cooling of the composite induces thermal forces. If the laminate is not symmetric, these forces will induce warping of the final part.

Failure Modes
-------------

The most popular criteria for composites failure are:

1. max stress criterion

2. max strain criterion

3. Tsai- Hill failure criterion

4. Tsai-Wu failure criterion

5. Truncated maximum strain criterion

Maximum Strain Criterion
------------------------

The maximum strain criterion is the most popular failure criterion in industry today. Using the concept of a strength ratio (load/strength) the strain criteria becomes. R=Strain/strain at break

Since elongations to failure are usually reported in percent values in the literature, they would have to be divided by 100 to be used.

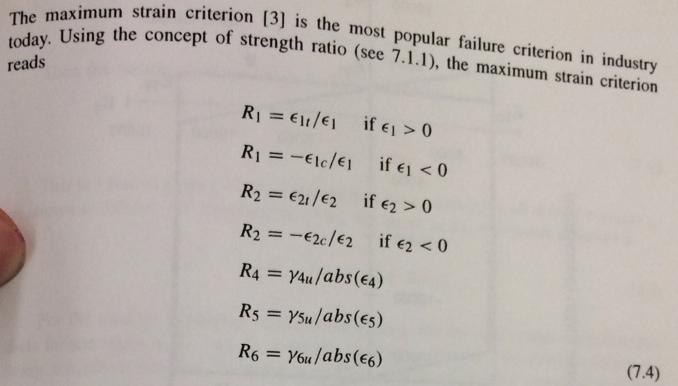
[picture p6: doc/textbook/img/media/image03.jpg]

------------------------------------------------------------

Truncated Max Strain Criterion
------------------------------

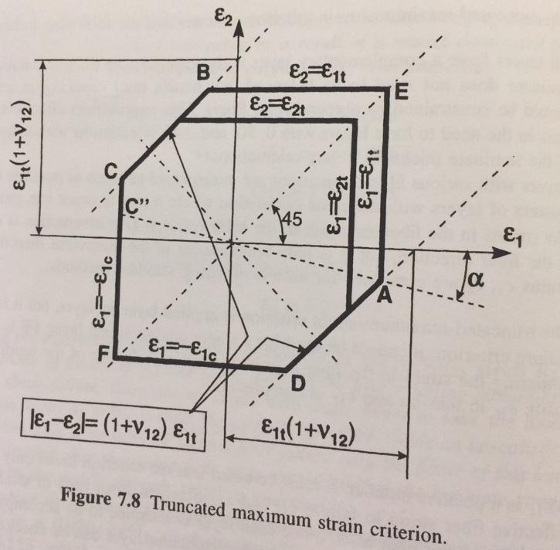
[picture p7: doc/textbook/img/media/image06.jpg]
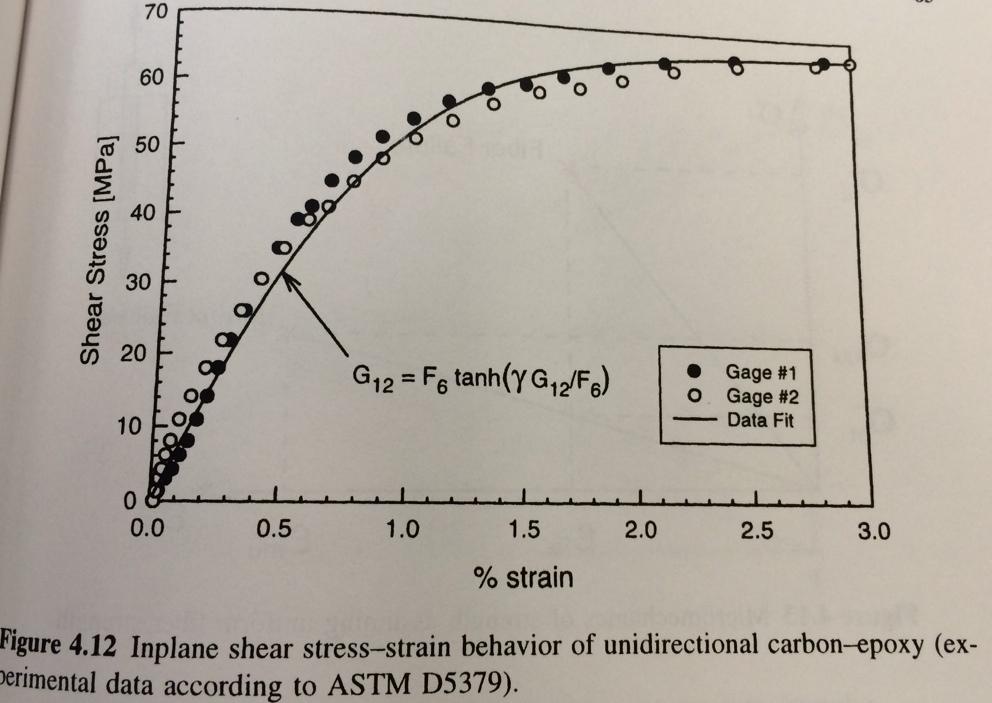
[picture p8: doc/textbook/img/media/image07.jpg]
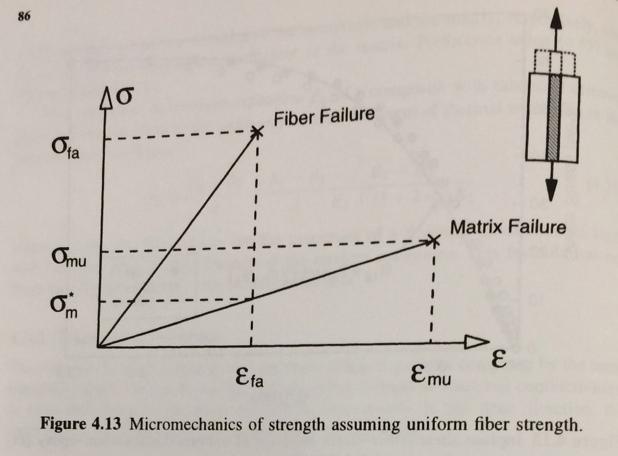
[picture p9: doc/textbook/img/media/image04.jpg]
The failure criterion can be summarized as to just checking every layer for fiber strain. This procedure is popular in the aerospace industry because of simplicity, and is reported to be quite accurate. The truncated maximum strain criterion goes one step further by limiting the strains in the tension compression quadrants to account for shear failure of the fibers. 

Thermoset Matrices
------------------

Undergo chemical change when cured. Process is not reversible. Low viscosity matrix material. Long 2 hour cure. Tacky pre preg. Relatively low processing temperature, good fiber wetting, formable into complex shapes. Requires refrigeration.

Filament
--------

The basic structural fibrous element. It is continuous, or at least very long compared to its average diameter, which is usually 5-10 microns.

Yarn
----

A small, continuous bundle of filaments, generally fewer than 10,000. The filaments are lightly stranded together so they can be handled as a single unit and may be twisted to enhance bundle integrity.

Tow
---

A large bundle of continuous filaments, not twisted. The number of filaments in a bundle is usually 3k, 6k, or 12k. 12k tow is the cheapest. 3K is the most expensive. The smaller tow sizes are normally used in weaving, winding, and braiding applications while large tow sizes are used in unidirectional tapes. Very thin tapes are also made from low filament-count tow for satellite applications.

Woven Fabrics
-------------

2D woven fabrics are more expensive than unidirectional tapes. However, significant cost savings are often realized in the manufacturing operation because layup labor requirements are reduced. Complex part shapes for processes require careful positioning of the reinforcement can benefit from the use of more handleable woven forms of fiber. Fabrics are generally described according to the types of weave and the number of yarns per inch, first in the warp direction (parallel to the length of the fabric, then in the fill direction( perpendicular to the warp).

Unidirectional fabrics
----------------------

Fabrics are essentially unidirectional and in these fabrics the reinforcements are oriented in one direction (warp) and held in position by tie yarns (fill) of a non structural nature which go over and under the structural fibers; the fibers (warp) lie straight with the same characteristics as tape.

Plain Weave
-----------

In this construction, one warp yarn is repetitively woven over one fill yarn and under the next. It is the firmest, most stable construction, which provides minimum slippage. Plain-weave fabrics are less flexible and are suitable for flat or simply-contoured parts; a slight sacrifice in fiber property translation occurs. Strength is uniform in both directoins.

Satin Weave
-----------

In this construction, one warp yarn is woven over several successive fill yarns, then under one fill yarn. A configuration haing one warp yarn passing over four and under one fill yarn is calld a 5 harness satin weave. Satin weaves are less open than other weaves and strength is high in both directions. In particular the commonly used 8 harness satin retains most of the fiber characteristics of tape ad can be easily draped over complex mold shapes.

Woven Fabrics
-------------

They are usually based on the more expensive 3k filament tows to ensure a thin uniform sheet. Because the fibers are necessarily kinked, the product cannot be expected to yield its full potential strength. Fiber discontinuities and overlapped splices are required. Lower fiber volume fraction than tapes. Greater scrap rates than tapes. Fabric distortion (bowing and skewing) causes part warping.

Sandwich core materials
-----------------------

The challenge of making a structure as light as possible without sacrificing strength is fundamental in aircraft design. Inevitably the requirement leads to the need to stabilize thin surfaces to withstand tensile and compressive loads and combinations of the two, in shear, torsion and bending. Traditional airframe structural design in has in the past, and does still to some extent, overcome this difficulty by the use of longitudinal stiffeners and stabilizing rings with stringers, and ribs or frames. But it is an inelegant solution and, in fact, the stabilization of a surface- creating a resistance to deforming forces- can be more efficiently effected by the use of twin skins with a stabilizing medium between them- what is now termed a sandwich structure. It is noteworthy, however, that scientific design has been paralleled, or rather anticipated, by nature and evolution, for the structure of the human skull bears a remarkable resemblance to a sandwich structure.

Potting compound
----------------

Potting compound is a low density material which has the following uses: material inserts, edge filling, preventing crushing by local concentrated loads in a honeycomb core, Joining material in honeycomb constructions, securing inserts installed in either honeycomb or foram core.

Release film
------------

These films are used to prevent the composite part from adhering to tool surfaces. Release film is also placed between the bleeder and breather plies as a separator film. It is used to prevent resin flow into the breather plies, to which the vacuum system vents. Resin in the vacuum system can clog it and break it. For resins that produce volatiles during cure or consolidation, a release film with small perforations which are widely spaced is used to prevent the breather from becoming clogged with resin and unable to perform its function. For resins that produce no volatiles during cure, an unperforated release film is frequently used so that resin removal can be controlled.

Peel ply
--------

Peel ply film or teflon coated fabric materials are placed on top of the layup serve to restrict but not prevent resin flow from the laminate. Most peel plies are porous or perforated and the size and spacing of perforations or the porosity of the material determines the amount of resin flow from the surface of the laid up laminate. If no resin removal during cure is desired, unperforated peel ply film should be used. The peel ply also serves to to control the surface roughness and finish of the composite. Surfaces that are to be adhesively bonded as a secondary operation after curing often use a peel ply to obtain a rough surface finish and also to keep them clean until ready for joining operation.

Bleeder ply
-----------

Bleeder plies are normally required to absorb excess resin and permit the escape of volatiles. Various solvents and other chmeicals in the prepreg that take part in the chemical reactoin during layups must be vented, or an unacceptably porous structure will result. There are basically two options:

1) Bleedout may occur through the edges (edge bleed). This is used on smaller parts (less than a foot) because there is a chance of bridging. Bagging costs are reduced due to the absence of bleeder, separator and vent cloths. There is less chance of surface wrinkles. It is much easier to debag when there is no bleeder to be removed. Considerations are: there is a greater chance of volatiles being left in the cured part. Variations in resin flow are very likely to result in the laminate being resin rich in the center and resin starved near the edges.

Caul plate
----------

A caul plate is a rigid smooth sheet or plate (metal or hard rubber material) with the same size and shape as the finished part and in direct contact with the composite layup in order to:

Provide a smooth bag side surface, prevent excessive resin washout, smooth the angle and prevent wrinkles at tapered areas, regulate configuration of joggles, prevent wrinkles and surface irregularities from forming when an elastomeric caul plate is used, most rubber cauls are used for high temperature thermoplastics, help distribute pressure evenly over the part.

Breather plies
--------------

Breather plies are usually fiberglass or synthetic fabric which is placed on top of the release film to allow dispersion of vacuum pressure over the layup and removal of entrapped air or volatiles during cure. Coarse, open weave fabrics are used, otherwise bridging and bag failure may occur.

Vacuum bags
-----------

the vacuum bag provides the means of removing vapors, and encouraging the required resin flow, so its design and implementation are important. The vacuum is used to assist removal of trapped air. The vacuum and pressure temperature cycles are adjusted to permit maximum removal of air, with maximum resin flow. The vacuum bag is the final item in a composite layup for autoclave or oven cure. The bag must be vacuum tight so no autoclave gas can enter the layup. Should bag or edge sealant failure occur, the autoclave gas enters the layup, neutralizing air and volatile removal. The choice of bag material and its compatibility with the tool shape and sealing arrangements are major decisions in the composites manufacturing process. Bags that are stretched too tight tend to leak, break or, on convex radii, span the layup, reducing effective pressure. In any event, leaks in the film or in the sealing of the bag are definitely unacceptable especially when curing thermoset parts because it results in the scrap of the part.

Vacuum/Vent lines
-----------------

Vacuum ports shall be placed beneath the vacuum bag or diaphragm at intervals which will ensure that any portion inside the layup laminate can be vented out through the lines. Some pressure/vacuum gauge are required to monitor the vacuum pressures. A vacuum of a minimum of 20 inches of mercury shall be used to check for leaks prior to autoclave processing. During the check, a loss of greater than 2 inches of mercury in 5 minutes is unacceptable.

Debulking
---------

When initially laid up, any number of plies are bound to trap a certain amount of air between them, and on contours their elasticity may prevent their laying smoothly on top of each other. The more plies that are laid up, the more likely it is that wrinkles will result and be cured into the laminate, resulting in an unacceptable laminate. A debulking procedure used in conjunction with squeezing the plies onto the tool surface is repeated as often as necessary during the layup of thick laminates to reduce rwrinkles and to fit the prepreg smoothly into the tool. However applying debulking on thin laminates or slightly contoured laminates results in little improvement in structural performance. Prior to cure, the layup laminate may need to be debulked under 20 inches Hg after every 5 to 10 plies are laid down. The debulking bagging arrangement usually conforms to to the general configuration.

Scarf joint
-----------

The shear stress in the adhesive of a scarf joint is virtually constant. This means that a sufficiently small scarf angle can be selected to provide 100% joint efficiency (the joint adhesive strength equals the laminate failure load). To insure that laminate failure occurs outside the joint (for optimum strength) the scarf angle should be between 6 and 10 degrees. At large angles, failure will occur prematurely. When extremely small scarf angles are used there is the danger of breaking off the tip of the stiffer laminate. Actual joint efficiencies are less than 100% because the manufacturing constraints often require angles greater than optimal.

Stepped lap joint
-----------------

Like the scarf joint, the stepped lap joint, offers considerably greater efficiencies for thick laminates than is possible with single and double lap joints. It has been used for composite to titanium bonded joints with both carbon and boron epoxy laminates. This joint shares some of the characteristics of both the double lap and scarf joints. The joint strength can be increased by increasing the number of steps and approximating more closely the scarf joint design. However, once the maximum number of steps possible has been attained by equalling the number of plies in the laminate, no further strength increase can be developed. Strength may be increased by tapering the outer adherends of the laminates in the overlap area so as to keep the combined adherend extensional stiffness essentially constant (by matching stiffnesses of adherends t) throughout the joint. If the adherend is thick enough to warrant this procedure, the design and fabrication methods should allow for it. Otherwise, the adhesive will be fully utilized only at one end of the joint. The critical detail in this joint design is the tail end of the thin step where fatigure failure is likely to occur. There are obvious problems of fit associated with both scarf and stepped lap joints if both laminates have been precured or machined.

Flush single strap joint
------------------------

Variations of this configuration are often found where a flush surface is needed. Highest peel stress of common joint types. Advisable to make ts&gt;t to reduce stresses due to moment even though it does increase eccentricity. increased overlap is very beneficial in reducing peel. Laminate ends should be tapered.

Bonded joints
-------------

In summary, adhesive bonding is most appropriate for thin laminates while mechanical fasteners are more suitable for thick laminates (unless a stepped lap joint is used). Bonding of structures provides an alternative to mechanically fastening assemblies. Some of the factors affecting joint strength are assembly types, layup and type of adhesive. Generally, adhesively bonded assembled structures are lighter and have reduced manufacturing and maintenance costs over mechanically fastened structures. Some characteristics of secondary bonding are: Requires excellent fit up, requires additional cure cycles, allows precured parts to be inspected prior to assembly.

For maximum effectiveness and confidence, adhesive bonds should be designed in accordance with following general principles: the bonded area should be as large as possible, a maximum percentage of the bonded area should contribute to the strength of the joint, the adhesive should be stressed in the direction of its maximum strength. The strength of bonded single lap and double lap joints depends primarily on the overlap length and the extensional stiffness of the laminates for a specific adhesive system. Theory and test have generally shown that the highest strength is attained when the value of Et \[laminate material modulus of elasticity (E) times its thickness (t)\] for the two laminates are equal to one another.

Bonded joint design guidelines
------------------------------

1.  Joints with short overlap lengths are more efficient in avoiding &gt; adhesive shear failure from peak shear stress

2.  To minimize peel stress consider the following

    1.  In double lap joints peel stress is a function of outer laminate &gt; bending stiffness

    2.  In unsupported single lap joints, peel stress is an inverse &gt; function of overlap

    3.  In eccentric joints, much larger overlaps are needed for shear &gt; strength are often required to allow alleviation of &gt; eccentricities by gentle deformations

    4.  taper ends to a thickness of about 30 thou and slope of 1/10

3.  Reduce joint eccentricity

4.  Do not use 90 degree plies on outer surfaces of the laminate (use 45 &gt; or 0 plies)

Cocuring
--------

One of the most attractive features of composite materials is that sections can be molded into complex shapes. Thus, panels that normally would have to be fabricated individually can often be cocured into single parts to eliminate the need for fasteners entirely. Cocuring will be defined as the curing of a laminate with stiffeners and attachments all in one process operation. There are many advantages to cocuring parts in airframe structures; in addition to the integrity of a one-piece construction, there are weight savings and most important is the savings in the cost of assembly labor. A typical commercial transport for example, may have as many as two million different types of fasteners. Thus the elimination of fasteners, which includes fastener cost and installation cost, can result in substantial savings.

Various combinations of resins can be cocured, but it is important to match the cure cycles, especially the temperature and speed of reaction. How the two resins react with each other must be examined, and they should be compatible, because the prepreg resin serves as the adhesive. Design considerations for cocuring include:

1.  Cocuring is inherently more complex, so there is a greater &gt; probability of a bad layup, with significantly more at risk.

2.  Misalignment of parts is possible, so tooling to hold the part &gt; properly becomes very important. As the component gets more &gt; complex, the parts are more difficult to keep in their proper &gt; place, therefore tooling needs to be more innovative.

3.  Part shrinkage during cooling must be accounted for. The tooling &gt; should have the same CTE as the part. Hence, composite tooling is &gt; preferred, especially for large parts.

4.  In cocuring, some areas are difficult to inspect because they &gt; are hidden.

5.  Controlling dimensions in center areas may be more difficult when &gt; cocuring

6.  If the part is too thick, applied heat combined with the heat &gt; generated from the chemical reaction may damage the part. &gt; Therefore the cure cycle should be adjusted to meet &gt; this phenomenon.

Composite to metal splice joining guidelines
--------------------------------------------

1.  Bonding composites to metals (consider thermal expansion)

    1.  Titanium (preferred)

    2.  steel (acceptable)

    3.  aluminum (not recommended) composite to aluminum (corrosion &gt; resistant aluminum) splice joints may be used under special &gt; circumstances

2.  Bonded step joints are preferred to scarf joints- more consistent &gt; results, design flexibility and lower costs for thicker laminate &gt; joints

3.  where possible, 0 degree plies should be placed adjacent to &gt; the bondline. 45 plies are also acceptable. 90 plies should never &gt; be placed adjacent to the bondline unless it is also the primary &gt; load direction.

4.  For a stepped joint, the metal thickness at the end step should be &gt; thick enough to prevent metal failure

5.  If possible, have 45 plies end on the first and last step of bonded &gt; step joints to reduce peak interlaminar shear stresses at the &gt; end steps.

6.  If possible, do not end too many of the 0 plies on any step surface &gt; to avoid peak stress

Moisture
--------

The absorption of moisture by the organic matrix of composites is an important factor at high temperatures. The moisture diffuses into the matrix, in both laminates and adhesives, causing them to swell and acts as a plasticizer or softener. The latter phenomenon is by far the most important for airframe applications and results in a decrease of the matrix glass transition temperature. This manifests itself in a decrease of matrix dominated properties at high temperatures. For example, compression strength is clearly reduced, but tension behavior is relatively unaffected, at the upper temperature ranges of the material’s usefulness. Composite mechanical properties are dependent upon the amount of water in the matrix and the temperature. Generally 350F composites absorb more moisture than 250F composites. thermosets absorb 1 to 2% moisture. Hot/wet conditions cause the matrix to become more plastic, cold/dry cause the matrix to become more brittle. Cyclical swelling and contracting due to recurring moisture exposure may lead to joint loosening. to minimize moisture egress, seal machined edges and surfaces of the laminates. Provide surface paint or protective coating. However, paint will not prevent moisture from diffusing into the composite matrix. When a part is not painted, a thin film of thermoset or thermoplastic resin should be applied to the surface to reduce porosity. Sealant should be applied when surfaces are exposed to weathering to reduce the effects of static rain, air oxidation, airblown sand and ultraviolet radiation.

Rain and sand erosion
---------------------

Erosion of composites edge results from exposure to rain, dust, and sand. Preventative measures for structures which will experiences long term exposure are:

1.  Aircraft leading edge components should be protected by rubberized &gt; coatings

2.  Composite surfaces such as leading edges of wing, horizontal or &gt; vertical stabilizers etc require some form of protection when &gt; exposed to the airstream. Wherever possible, the best protection &gt; for leading edge composites is a metallic outer layer. other &gt; protection choices include:

    1.  use of paint or elastomeric/metallic coatings

    2.  application of a polyurethane (which has shown satisfactory &gt; results on thermosets)

3.  Forward facing edges of laminates which are exposed to the airstream &gt; are especially vulnerable and should be protected with edge wrap &gt; film or an anti peel ply

Galvanic corrosion
------------------

The aircraft industry has vast amounts of data gained from history and research on corrosion to design out corrosion and to manufacture corrosion resistant airframes. galvanic corrosion occurs where two materials from different groups in the galvanic series, are in contact in the presence of moisture. This type of corrosion is usually accompanies by a buildup of corrosion products in the contact area. Corrosion progresses more rapidly the further apart the materials are in the galvanic series. For example, aluminum will corrode when in contact with carbon composites. This is especially a problem with the mechanical fasteners generally used in assemblies. Galvanic corrosion can be reduced by insulating the materials in the areas of contact and by applying protective coatings on both materials. Recommendations:

1.  Carbon composites in contact with metals

    1.  Carbon will induce corrosion when in contact with aluminum when &gt; moisture exists, unless moisture intrusion is prevented

    2.  Keep carbon composites out of electrical contact with any &gt; adjacent metals

    3.  Carbon is highly cathodic and will severely attack aluminum and &gt; cadmium unless a protective ply of inert cloth (fiberglass &gt; kevlar etc) is used between them and or protective paint or &gt; sealant is used.

2.  If an aluminum part is to be used in contact with carbon parts, all &gt; aluminum and carbon parts should be processed as follows prior to &gt; assembly:

    1.  Method A

        1.  Anodize aluminum parts per MIL-A-8615, type II

        2.  Finish external surfaces of both aluminum and carbon parts &gt; per MIL-F-18264

        3.  Two coats of epoxy primer per MIL-P-85582

        4.  Two coats of white polyurethane enamel per MIL-C-83286

    2.  Method B

        1.  Cure a layer of fiberglass ply to the composite interface

        2.  Seal edges of composites

3.  Do not use cadmium plated fasteners in carbon composites, install &gt; fasteners wet with corrosion inhibiting sealant

### Honeycomb Core

Honeycomb is used extensively in composite panels to add bending stiffness with very little mass penalty. The panel facesheets carry tensile and compressive loads, and the honeycomb carries transverse stresses. In a highly loaded panel, the transverse stresses may approach the strength of the honeycomb. Thus, it is important to use the correct properties when designing a panel.

This issue comes up in the shop every once in a while, and I am always surprised when someone does not realize that honeycomb transverse shear properties are dependent upon direction. The two in-plane directions on a panel are called the "L" or ribbon direction and the "W" or transverse-to-ribbon direction. The shear modulus and strength in the ribbon direction are roughly twice that in the transverse direction.

These directions may seem difficult to keep track of, but it is really very easy. All you need to know is how honeycomb is manufactured. After that, you will be able to look at a panel and instantly pick out the ribbon direction, and you will have no trouble remembering which direction is the strongest and stiffest.

Honeycomb starts out as flat strips of material, or ribbons. Strips of adhesive are placed on the ribbons in a staggered pattern.



Next, the sheets are stacked together and cured.



Once cured, the blocks are cut to the desired thickness, and then the ribbons are pulled apart or expanded to form honeycomb.

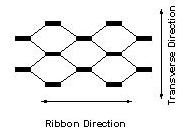
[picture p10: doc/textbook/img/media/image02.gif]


Fully expanded honeycomb forms the familiar hexagon shape. The expansion can be stopped before the hexes are fully formed (underexpanded core) or stopped after the hexes are fully formed (overexpanded or OX core). OX-core cells actually look more like rectangles than I have drawn here.

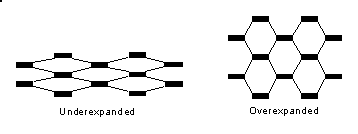
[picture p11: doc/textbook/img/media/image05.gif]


Normal honeycomb cannot be "bent" very much to form to contours. Underexpanded and overexpanded core can be formed to moderate contours in one direction. For complex, compound contours, Hexcel makes a core called Flex-Core which actually has higher properties when curved than when flat (the shape of the cells is also not hexagonal).

By now, it should be obvious why honeycomb is stronger and stiffer in the warp direction.

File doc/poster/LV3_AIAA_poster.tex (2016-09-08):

\documentclass[slidestop, compress]{beamer} % Adjust the font scale/size here

\title{Design and Manufacture of an Open-Hardware University Rocket Airframe using Carbon Fiber}
\author{Joe Shields \and Leslie Elwood }
\footer{For more info, visit }

\begin{document}
asdf
\begin{frame}
\lipsum
\end{frame}

\begin{block}{title}
	\lipsum
\end{block}

\end{document}

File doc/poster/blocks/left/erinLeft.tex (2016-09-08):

\documentclass[8pt]{beamer}
\usepackage[orientation=portrait,size=custom, width=21, height=18]{beamerposter}
% \usetheme{simple}
\setbeamertemplate{navigation symbols}{}
\usetheme{default}
\usecolortheme{beaver}
\setbeamersize{text margin left=5pt,text margin right=5pt}

\usepackage{lmodern}
%\usepackage[scale=2]{ccicons}

% TODO: 
%   position adjustement
%   change colours
%       

% Watermark background (simple theme)

\begin{document}

\begin{frame}[plain]
\begin{itemize}
\item Need more drop-tests: complete Bode diagram to improve dynamical model, further controller design iterations
\item State determination with sensor fusion via Kalman filtering suntracker, magnetometer, and gyroscopes
\end{itemize}
\tiny
\parbox{10in}{
The amateur and university rocketry communities are rapidly reaching higher altitudes with more sophisticated rockets. However, most groups are still using heavy airframes made of metal or fiberglass. Commercial off-the-shelf airframes are either too expensive for low-budget university groups or too small to use as a platform for high altitude experiments. 
A capstone team of mechanical engineering seniors at Portland State University has developed a low-weight, modular carbon fiber airframe as an open-hardware technology for university rocketry. 
This project continues the work of a 2014 capstone team, who developed a carbon fiber layup process with promising results. 
This will enable low-budget groups like the Portland State Aerospace Society to explore high altitude science and compete in the university space race.  

\begin{figure}[h]
\def\svgwidth{10in}
\input{moduleDiagram.pdf_tex}
\caption{
	Diagram of the male end of a module. 
	The CF (1) is bonded to the honeycomb core (3) and the aluminum coupling ring (4) using structural adhesive (2). 
	The adhesive also serves as a protective coating for the CF and provides a smooth outer surface. 
	See figure \ref{fig:coupon} for a picture of this design.
	}
\label{fig:moduleDiagram}
\hfill
\input{coupon.pdf_tex}
\caption{
	A cut-away sample displaying the layers used in the LV3 sandwich shells. 
	See figure \ref{fig:moduleDiagram} for a diagrammatic depiction.
	}
\label{fig:coupon}
\end{figure}
}
\end{frame}

\end{document}

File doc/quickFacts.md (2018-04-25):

Figures in _italics_ are predictions.

# Launch 13
(Updated 2018-03-01)

## Operations
- Apogee: _18 000 ft (5.5 km)_
- Time to apogee: _32 s_
- Max speed: _950 mph (425 m/s, Mach 1.3)_
- Max acceleration: _10.75 G (105 $m/s^2$)_
- Times flown: 0

## Airframe
- Length: 11' 6.9" (3.528 m)
- Outer diameter: 6.6" (168 mm)
- Max Thrust: _787 $lb_f$ (3.5 kN)_
- Propellant:
- Dry mass: _48 $lb_m$ (21.8 kg)_
- Wet mass: _67.25 $lb_m$ (30.5 kg)_
- subsystems
	- eNSR: electromechanical nosecone separation ring
	- parachute recovery
	- carbon composite airframe manufactured at PSU
	- 360 degree camera module (six cameras at 1080p, 60 fps)
	- Telemetrum for altitude determination
	- temperature logging at points of interest

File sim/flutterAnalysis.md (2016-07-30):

The following is a shot at estimating the factor of safety against flutter for the LV3 fins, using different materials and fin thicknesses. The data for air pressure, speed of sound, and airspeed come from OpenRocket (OR) simulations of the corresponding fin thicknesses. We could use a better model (see assumptions section), so I wrote this to be pretty much agnostic of the formula used to calculate the critical flutter velocity defined at the top of the script.

[Here is the source](http://ntrs.nasa.gov/archive/nasa/casi.ntrs.nasa.gov/19930085030.pdf) for this equation. (page 14, equation 18)

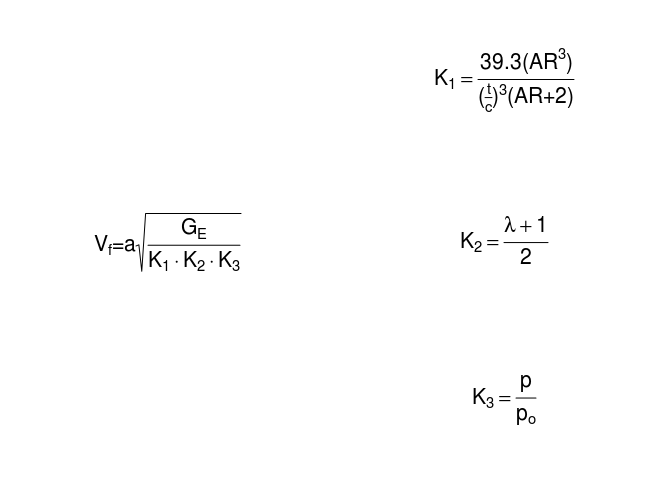
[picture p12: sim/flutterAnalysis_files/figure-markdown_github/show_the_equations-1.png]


    ## NULL

| Symbol | Meaning | Variable |
|---|---|---|
| *V*<sub>*f*</sub> | Flutter Velocity (m/s) | vel.flutter() |
| *a* | Speed of Sound (m/s) | vel.sonic |
| *G*<sub>*E*</sub> | Effective Shear Modulus (Pa) | mod.shear |
| *A**R* | Aspect Ratio | asp |
| *t* | Fin Thickness (m) | thick |
| *c* | Fin Chord (m) | chord |
| *λ* | Taper Ratio (Tip Chord to Root Chord) | taper |
| *p* | Air Pressure (Pa) | press |
| *p*<sub>*o*</sub> | Air Pressure, Sea Level (Pa) | press0 |

Assumptions of this model
-------------------------

-   high aspect ratio fins (2:3) **\[violated\]**
-   low ratio of bending frequency to torsional frequency (can get from SW) **\[???\]**
-   heavy fins **\[???\]**
-   constant airfoil geometry along the fin (the airfoil is a *very* thin rupee at the root and a thin rupee at the tip) **\[violated\]**
-   the center of mass is around the center of the fin (can get from SW) **\[probably violated\]**
-   the fluid is air **\[OK\]**
-   solid airfoil **\[violated\]**
-   thin airfoil (slenderness is 1:20 at the tip) **\[OK\]**
-   no struts in the frame (conservative) **\[OK\]**
-   stationwise frame profiles are square (conservative) **\[OK\]**
-   stationwise cross sections of the frame beams are small compared to the chord length (1:20 at the tip) **\[OK\]**

Since there are a few violated assumptions for equation 18, we should probably switch to one of the earlier equations in the paper, before these assumptions are brought in.

I recommend we switch either to equation 1, since we can estimate *ω*<sub>*α*</sub> and *x*<sub>*α*</sub> using Solidworks, or try to find a relation that is valid for low aspect ratio fins (*c*<sub>0.5</sub>/*L* = 1.8).

Code-y stuff
------------

#### define the function for critical flutter velocity

Fortunately, if we decide we want to use some other estimate of the critical flutter velocity, we can just change this function, and not muck around with the rest of the script.

``` r
vel.flutter <- function(vel.sonic, mod.shear, asp, thick, chord, taper, press, press0)
{
    K1 <- 39.3*asp^3/((thick/chord)^3*(asp+2))
    K2 <- (taper+1)/2
    K3 <- press/press0
    return(vel.sonic*sqrt(mod.shear/(K1*K2*K3)))
}
```

#### define the parameters

The information on the planform is just copied from OR. The sealevel pressure is from basically any reference. The thicknesses are plausible thicknesses we could buy. The modulus of rigidity for aluminum comes from [here](http://www.engineeringtoolbox.com/modulus-rigidity-d_946.html). The modulus for fiberglass is based off of [a PCB listed on MatWeb](http://www.matweb.com/search/DataSheet.aspx?MatGUID=952559b637a940658f6ab71767504fdc) and is low for many of the glass-based composites listed.

``` r
chord.root <- 18*25.4/1e3 # m, converted from inches
chord.tip <- 5*25.4/1e3 # m, converted from inches
semispan <- 6.4*25.4/1e3 # m, converted from inches
# mod.shear <- 24e9 # Pa, shear modulus for aluminum
press0 <- 101e3 # Pa, atmospheric pressure at sealevel
CSVs <- c("simData/L-13a_ideal_0.25fins.csv", "simData/L-13a_ideal_0.125fins.csv", "simData/L-13a_ideal_0.09375fins.csv", "simData/L-13a_ideal_0.0625fins.csv") # names of the OR outputs
thicknesses.inch <- c(1/4, 1/8, 3/32, 1/16) # inches (gets converted to meters later)
materials <- c("aluminum", "fiberglass") # material names
mod.shears <- c(24e9, 2e9) # Pa, moduli of rigidity for the materials
```

#### secondary parameters

``` r
chord.mean <- (chord.root+chord.tip)/2 # m, mean chord length
asp <- semispan/chord.mean # m, planform aspect ratio
taper <- chord.tip/chord.root # dimensionless taper ratio
```

#### create a function to read the OR output and add in the flutter information

To simplify the problem, I assumed there were no struts in the frame. I also assumed that the stationwise profile of the frame was two squares (one for the leading edge, and another for the trailing edge) with the given thickness. These are both conservative approximations, since the actual fin will have beefier geometry and therefore be more rigid.

I also approximate the polar moment of inertia as being determined by the two "point areas" of the squares (you'll hopefully see what I mean in the calculation), rather than integrating out those two dinky little squares. Essentially, I'm assuming that the squares are small compared to the chord, which they are. (1:20 at the tip)

``` r
analyze.flutter <- function(csv, thick, mod.shear)
{
    #read in the data
    dat <- read.csv(csv, comment.char = "#")
    
    #fix the variable names
    lines <- readLines("simData/L-13a_ideal_0.25fins.csv")
    varNames <- unlist(strsplit(lines[7], ","))
    varNames <- gsub(pattern = "# ", replacement = "", x = varNames)
    varNames <- gsub(pattern = " ", replacement = "_", x = varNames)
    varNames <- gsub(pattern = "\\(", replacement = "", x = varNames)
    varNames <- gsub(pattern = "\\)", replacement = "", x = varNames)
    names(dat) <- varNames
    
    # find the secondary parameters
    polar.moment <- chord.mean^2*thick^2/2 # approximation, assuming a frame with no struts and a square cross section, using "point areas"
    polar.moment.rect <- chord.mean*thick*(chord.mean^2+thick^2)/12
    mod.shear.eff <- polar.moment*mod.shear/polar.moment.rect
    
    # find the critical flutter velocity at every point in time
    for (i in 1:length(dat$Time))
    { 
        # assign the flutter velocity to a new variable in the data frame
        dat$vel.flutter[i] <- vel.flutter(
                vel.sonic = dat$`Speed_of_sound_m/s`[i],
                mod.shear = mod.shear.eff,
                asp = asp,
                thick = thick, 
                chord = chord.mean, 
                taper = taper, 
                press = dat$Air_pressure_Pa[i], 
                press0 = press0
            )
        #assign the factor of safety to a new variable in the data frame
        dat$FS.flutter[i] <- dat$vel.flutter[i]/dat$Vertical_velocity[i]
        # get rid of things that aren't actual numbers
        if (is.infinite(dat$FS[i])) 
            dat$FS.flutter[i] <- NA
    }
    return(dat)
}
```

I also wrote a function to plot the data and find the factor of safety, but that's just a bunch of book-keeping. You can check the `.Rmd` source if you want to see it.

The current design (aluminum, 1/4" thick)
-----------------------------------------

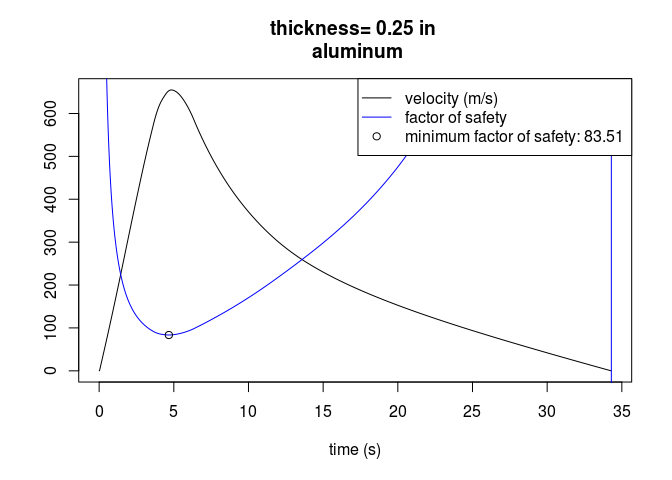
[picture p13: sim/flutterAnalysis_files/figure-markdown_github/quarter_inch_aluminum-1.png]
So, let's check out the flutter factor of safety for the current fins (with no struts and a simplified frame). 

    ## [1] 83.51251

Okay, it's clear that this design is *way* overbuilt for flutter. The FS is on the same scale as the velocity... This means we can start to play around with thinner fins and lighter materials.

Different thicknesses of aluminum and fiberglass
------------------------------------------------

The following factors of safety are for 1/4", 1/8", 3/32", and 1/16" frames of aluminum and fiberglass.

    ## 
    ## ----- aluminum -----
    ## factor of safety for 0.25 inch thick aluminum = 83.51251 
    ## factor of safety for 0.125 inch thick aluminum = 20.88183 
    ## factor of safety for 0.09375 inch thick aluminum = 11.45416 
    ## factor of safety for 0.0625 inch thick aluminum = 5.09083 
    ## 
    ## ----- fiberglass -----
    ## factor of safety for 0.25 inch thick fiberglass = 24.10799 
    ## factor of safety for 0.125 inch thick fiberglass = 6.028064 
    ## factor of safety for 0.09375 inch thick fiberglass = 3.30653 
    ## factor of safety for 0.0625 inch thick fiberglass = 1.469596

Thoughts/conclusions
--------------------

If we're to believe the above analysis, we're pretty much free to make the fins as thin as we want, especially since the carbon and struts will make the fin more rigid.

However, The FS for the 1/16" FG frame makes me question the results. Remember that a 1/16" fiberglass plate is a PCB. This is essentially the consideration of a fin frame made of 1/16" diameter fiberglass rods. Of course, I'm intuitively imagining the frame "crumpling" under a torsional load, which a plate -- which the model is based on -- would not do. There's also a video (can't seem to re-find it) of a guy's rocket surviving flutter, where he later shows that he can bend the fins by hand. That result would indicate to me that if you can bend the fins, there's a good chance they'll flutter.

I also still don't understand how the density of the fins falls out of the the analysis in the NASA paper. It seems like you could always stave off flutter by making heavier fins, thereby raising their natural frequency (maybe that's the reason for the "heavy fin" assumption). I'm sure it would help if I read through the paper more carefully.

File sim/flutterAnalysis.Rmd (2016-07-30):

---
title: "Flutter Analysis for LV3"
author: "Joe Shields, Ian Zabel"
date: "July 26, 2016"
---

```{r, joe_wd, echo=F}
#setwd("~/Github/PSAS/sw-cad-airframe-lv3.0/sim")
```

The following is a shot at estimating the factor of safety against flutter for the LV3 fins, using different materials and fin thicknesses. The data for air pressure, speed of sound, and airspeed come from OpenRocket (OR) simulations of the corresponding fin thicknesses. We could use a better model (see assumptions section), so I wrote this to be pretty much agnostic of the formula used to calculate the critical flutter velocity defined at the top of the script. 

[Here is the source](http://ntrs.nasa.gov/archive/nasa/casi.ntrs.nasa.gov/19930085030.pdf) for this equation. (page 14, equation 18)

```{r, show_the_equations, echo=F, message=F}
# install.packages("latex2exp")
require("latex2exp")
par.old <- layout(matrix(c(1,1,1,2,3,4), 3, 2, byrow = F))
par(mar=c(0,0,0,0), mai=c(0,0,0,0))
latexStr <- c(
	"$V_{f}=a \\sqrt{\\frac{G_{E}}{K_{1} \\cdot K_{2} \\cdot K_{3}}}$",
	"$K_{1}=\\frac{39.3(AR^3)}{(\\frac{t}{c})^3 (AR+2)}$",
	"$K_{2}=\\frac{\\lambda+1}{2}$",
	"$K_{3}=\\frac{p}{p_{o}}$"
	)
for (i in 1:length(latexStr))
{
	plot.new()
	text(
		x = 0.5, y= 0.5, cex = 2, 
		labels = TeX(latexStr[i])
	)
}
par(par.old)
# $V_{f}=a \sqrt{\frac{G_{E}}{K_{1}*K_{2}*K_{3}}}$  
# $K_{1}=\frac{39.3(AR^3)}{(\frac{t}{c})^3 (AR+2)}$  
# $K_{2}=\frac{\lambda+1}{2}$  
# $K_{3}=\frac{p}{p_{o}}$  
```

Symbol|Meaning|Variable
-----|-----|-----
$V_{f}$		|	Flutter Velocity (m/s)			|	vel.flutter()
$a$ 		|	Speed of Sound (m/s)			|	vel.sonic
$G_{E}$ 	|	Effective Shear Modulus (Pa)		|	mod.shear
$AR$		|	Aspect Ratio				|	asp
$t$		|	Fin Thickness (m)			|	thick
$c$		|	Fin Chord (m)				|	chord
$\lambda$	|	Taper Ratio (Tip Chord to Root Chord)	|	taper
$p$		|	Air Pressure (Pa)			|	press
$p_{o}$		|	Air Pressure, Sea Level (Pa)		|	press0

## Assumptions of this model
* high aspect ratio fins (2:3) __[violated]__
* low ratio of bending frequency to torsional frequency (can get from SW) __[???]__
* heavy fins __[???]__
* constant airfoil geometry along the fin (the airfoil is a _very_ thin rupee at the root and a thin rupee at the tip) __[violated]__
* the center of mass is around the center of the fin (can get from SW) __[probably violated]__
* the fluid is air __[OK]__
* solid airfoil __[violated]__
* thin airfoil (slenderness is 1:20 at the tip) __[OK]__
* no struts in the frame (conservative) __[OK]__
* stationwise frame profiles are square (conservative) __[OK]__
* stationwise cross sections of the frame beams are small compared to the chord length (1:20 at the tip) __[OK]__

Since there are a few violated assumptions for equation 18, we should probably switch to one of the earlier equations in the paper, before these assumptions are brought in.

I recommend we switch either to equation 1, since we can estimate $\omega_\alpha$ and $x_\alpha$ using Solidworks, or try to find a relation that is valid for low aspect ratio fins ($c_{0.5}/L=1.8$).

## Code-y stuff
#### define the function for critical flutter velocity
Fortunately, if we decide we want to use some other estimate of the critical flutter velocity, we can just change this function, and not muck around with the rest of the script.
```{r, define_empirical_equation}
vel.flutter <- function(vel.sonic, mod.shear, asp, thick, chord, taper, press, press0)
{
	K1 <- 39.3*asp^3/((thick/chord)^3*(asp+2))
	K2 <- (taper+1)/2
	K3 <- press/press0
	return(vel.sonic*sqrt(mod.shear/(K1*K2*K3)))
}
```

#### define the parameters
The information on the planform is just copied from OR. The sealevel pressure is from basically any reference. The thicknesses are plausible thicknesses we could buy. The modulus of rigidity for aluminum comes from [here](http://www.engineeringtoolbox.com/modulus-rigidity-d_946.html). The modulus for fiberglass is based off of [a PCB listed on MatWeb](http://www.matweb.com/search/DataSheet.aspx?MatGUID=952559b637a940658f6ab71767504fdc) and is low for many of the glass-based composites listed. 
```{r, define_primary_parameters}
chord.root <- 18*25.4/1e3 # m, converted from inches
chord.tip <- 5*25.4/1e3 # m, converted from inches
semispan <- 6.4*25.4/1e3 # m, converted from inches
# mod.shear <- 24e9 # Pa, shear modulus for aluminum
press0 <- 101e3 # Pa, atmospheric pressure at sealevel
CSVs <- c("simData/L-13a_ideal_0.25fins.csv", "simData/L-13a_ideal_0.125fins.csv", "simData/L-13a_ideal_0.09375fins.csv", "simData/L-13a_ideal_0.0625fins.csv") # names of the OR outputs
thicknesses.inch <- c(1/4, 1/8, 3/32, 1/16) # inches (gets converted to meters later)
materials <- c("aluminum", "fiberglass") # material names
mod.shears <- c(24e9, 2e9) # Pa, moduli of rigidity for the materials
```

#### secondary parameters
```{r, calculate_secondary_parameters}
chord.mean <- (chord.root+chord.tip)/2 # m, mean chord length
asp <- semispan/chord.mean # m, planform aspect ratio
taper <- chord.tip/chord.root # dimensionless taper ratio
```

#### create a function to read the OR output and add in the flutter information
To simplify the problem, I assumed there were no struts in the frame. I also assumed that the stationwise profile of the frame was two squares (one for the leading edge, and another for the trailing edge) with the given thickness. These are both conservative approximations, since the actual fin will have beefier geometry and therefore be more rigid. 

I also approximate the polar moment of inertia as being determined by the two "point areas" of the squares (you'll hopefully see what I mean in the calculation), rather than integrating out those two dinky little squares. Essentially, I'm assuming that the squares are small compared to the chord, which they are. (1:20 at the tip)
```{r, flutter_calculation_function}
analyze.flutter <- function(csv, thick, mod.shear)
{
	#read in the data
	dat <- read.csv(csv, comment.char = "#")
	
	#fix the variable names
	lines <- readLines("simData/L-13a_ideal_0.25fins.csv")
	varNames <- unlist(strsplit(lines[7], ","))
	varNames <- gsub(pattern = "# ", replacement = "", x = varNames)
	varNames <- gsub(pattern = " ", replacement = "_", x = varNames)
	varNames <- gsub(pattern = "\\(", replacement = "", x = varNames)
	varNames <- gsub(pattern = "\\)", replacement = "", x = varNames)
	names(dat) <- varNames
	
	# find the secondary parameters
	polar.moment <- chord.mean^2*thick^2/2 # approximation, assuming a frame with no struts and a square cross section, using "point areas"
	polar.moment.rect <- chord.mean*thick*(chord.mean^2+thick^2)/12
	mod.shear.eff <- polar.moment*mod.shear/polar.moment.rect
	
	# find the critical flutter velocity at every point in time
	for (i in 1:length(dat$Time))
	{ 
		# assign the flutter velocity to a new variable in the data frame
		dat$vel.flutter[i] <- vel.flutter(
				vel.sonic = dat$`Speed_of_sound_m/s`[i],
				mod.shear = mod.shear.eff,
				asp = asp,
				thick = thick, 
				chord = chord.mean, 
				taper = taper, 
				press = dat$Air_pressure_Pa[i], 
				press0 = press0
			)
		#assign the factor of safety to a new variable in the data frame
		dat$FS.flutter[i] <- dat$vel.flutter[i]/dat$Vertical_velocity[i]
		# get rid of things that aren't actual numbers
		if (is.infinite(dat$FS[i])) 
			dat$FS.flutter[i] <- NA
	}
	return(dat)
}
```
I also wrote a function to plot the data and find the factor of safety, but that's just a bunch of book-keeping. You can check the `.Rmd` source if you want to see it.
```{r, plot_and_FS_func, echo=F}
plot.flutter <- function(csv, thick, show.plot=T, mod.shear, material)
{
	# get the spiced-up data frame
	dat <- analyze.flutter(csv=csv, thick=thick, mod.shear=mod.shear)
	# find the regions between launch and appogee and the supersonic region, respectively
	ind.flight <- which(dat$`Vertical_velocity_m/s`>0)
	ind.ss <- which(dat$`Mach_number`>1) # when it's super sonic
	
	if (show.plot){# kind of a redundant check
		# plot the velocity over time
		plot(
			dat$Time[ind.flight], dat$Vertical_velocity[ind.flight], 
			type="l",
			xlab= "time (s)",
			ylab= NA,
			main= paste(
				"thickness=", formatC(thick*1e3/25.4, digits=3), "in",
				"\n", material
				)
			)
		# add in the factor of safety
		lines(
			dat$Time, dat$FS, 
# 			type="l",
			col="blue"
# 			xlab= "time (s)", ylab= NA,
# 			ylim= c(0, 85),
# 			main= paste(
# 				"thickness=", formatC(thick*1e3/25.4, digits=3), "in",
# 				"\n", material
# 				)
			)
		# add a point showing the overall factor of safety for this configuration
		points(dat$Time[ind.ss][which.min(dat$FS[ind.ss])], min(dat$FS[ind.ss]))
		# add a legend
		legend(
			"topright", 
			legend=c(
				"velocity (m/s)",
				"factor of safety",
				paste(
					"minimum factor of safety:",
					formatC(min(dat$FS[ind.ss]), width = 2)
					)
				),
			pch= c(NA, NA, 1),
			lty= c(1, 1, NA),
			col= c("black", "blue", "black")
			)
	}
	# return the overall factor of safety
	return(min(dat$FS[ind.ss]))
}
```

## The current design (aluminum, 1/4" thick)
So, let's check out the flutter factor of safety for the current fins (with no struts and a simplified frame).
```{r, quarter_inch_aluminum, echo=F, message=F}
# plot dat shit, but don't echo or show the output; just the plot
plot.flutter(
		csv= "simData/L-13a_ideal_0.25fins.csv", 
		thick= thicknesses.inch[1]*25.4/1e3, 
		mod.shear=mod.shears[1],
		material= materials[1]
		)
```
Okay, it's clear that this design is _way_ overbuilt for flutter. The FS is on the same scale as the velocity... This means we can start to play around with thinner fins and lighter materials. 

## Different thicknesses of aluminum and fiberglass
The following factors of safety are for 1/4", 1/8", 3/32", and 1/16" frames of aluminum and fiberglass.
```{r, many_thicknesses_and_materials, echo=F, fig.show="hide", message="hold"}
# Do the same for all the materials and thicknesses. Don't show the code or plots, just the output.
for (j in 1:length(materials))
{
	cat("\n-----", materials[j], "-----\n")
	for (i in 1:length(CSVs))
	{
		cat(
			"factor of safety for", thicknesses.inch[i] , 
			"inch thick", materials[j], "=",
			plot.flutter(
				csv= paste(
					"simData/L-13a_ideal_", 
					as.character(thicknesses.inch[i]), 
					"fins.csv", sep=""
					), 
				thick= thicknesses.inch[i]*25.4/1e3, 
				mod.shear=mod.shears[j],
				material= materials[j],
				show.plot = F
				),
			"\n"
			)
	}
}
```

## Thoughts/conclusions
If we're to believe the above analysis, we're pretty much free to make the fins as thin as we want, especially since the carbon and struts will make the fin more rigid. 

However, The FS for the 1/16" FG frame makes me question the results. Remember that a 1/16" fiberglass plate is a PCB. This is essentially the consideration of a fin frame made of 1/16" diameter fiberglass rods. Of course, I'm intuitively imagining the frame "crumpling" under a torsional load, which a plate -- which the model is based on -- would not do. 
There's also a video (can't seem to re-find it) of a guy's rocket surviving flutter, where he later shows that he can bend the fins by hand. That result would indicate to me that if you can bend the fins, there's a good chance they'll flutter.

I also still don't understand how the density of the fins falls out of the the analysis in the NASA paper. It seems like you could always stave off flutter by making heavier fins, thereby raising their natural frequency (maybe that's the reason for the "heavy fin" assumption). I'm sure it would help if I read through the paper more carefully.

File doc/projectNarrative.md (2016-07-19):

# Narrative of the LV3 airframe 2016 capstone

## Introduction

The following is essentially a description of the LV3 airframe project sorted by subject.
It also includes thoughts about what worked well, what didn't, how it could have been better, and how we would do it differently.
For a chronological description, see the [project updates](/updates/).

The LV3 team set out to build an airframe according to the following requirements, in fulfillment of a mechanical engineering capstone.

1. Design and manufacture airframe to work up to Mach 3. (We later determined that it would realistically only ever see Mach 2.)
	1. Reproduce the results from the 2014 capstone in making cylindrical modules.
	1. Design and manufacture a nose cone with a metal tip.
	1. Design and manufacture a fin can with metal leading edges.
1. Destructively test at least one copy of every part.
1. Create one full airframe and one backup airframe.
1. Create clear how-to documentation for future builds.

If you don't read anything else in this document:

* __Put all desicions and tasks in writing.__ Email is OK. Weekly logs are better. Both is preferred. When in doubt, CC some more people.
* __Confirm everything with someone__, even if you know what you're doing, *especially* if you don't. 
* __Read/learn what people tell you to.__ If a rocket without a turboencabulator explodes, *you'd better know what one is!*
* __Do the calculation.__ Your intuition is wrong. You have time to not ruin everything.
* __Go to every meeting.__ The people at PSAS know things you don't. Talk to them. 

If you didn't read anything else though... you'd be such a scrub.

## Materials

Perhaps the biggest stumbling block in the project was the materials. 
Essentially the whole first half of the project was spent dealing with materials. 

In addition the problems acquiring materials, we had problems with the materials themselves. "Reproduce the results from the 2014 capstone in making cylindrical modules," isn't as simple as it sounds. 
The techniques developed by the 2014 team were for their specific materials. So, we ended up needing to reformulate a few key pieces. In the end, we got a procedure and design that was *similar* to the 2014 version.
One very troublesome part of this was that we always thought that we were one issue away from reproducing their results. 
The takeaway from this is that unless you have a finished part sitting in front of you, there are no guarantees that you will get that part soon.

We acquired donations of carbon fiber (CF) and fiberglass (FG) from Pacific Coast Composites (PCC) (contact: ??). They also gave us adhesive, but it wasn't a full roll, and it wasn't a kind of adhesive that was useful in our design.
Similar things will undoubtedly happen to future groups working with CF. The necessary materials are prohibitively expensive, so you have to rely on donations. 
This means that you don't necessarily get what you want or need. 

At the end of the winter term, we were all but convinced that the other carbon fiber team (LV4 aka NGCF) would need to massively reduce the scope of their project, due to a lack of adhesive.
Luckily, we got a huge donation from Boeing (contact: [Loren Coleman](mailto:loren.m.coleman@boeing.com) and [Sandie Hallman](mailto:sandie.h.hallman@boeing.com)) which included the proper Meltbond 1515 adhesive. They also gave us huge amounts of vacuum bagging supplies, prepreg FG, and prepreg CF (plain weave and unidirectional).
Boeing, being a *huge* company, often gets rid of stock that is expired or in excess. It's sporadic and you have to periodically ask them what they've got, but you can get huge amounts of new (for our purposes) material this way.

In fact, we ended up creating a different problem for ourselves. We then had so much material that we didn't have space for it. 
At that time, we only had the Viking Motor Sports (VMS) freezer to store material in. Note that it's not even long enough to store some rolls.
We had to scramble to get a freezer to store all our material in (MME was not super enthusiastic about buying it).
The biology department was gracious enough to let us store a lot of it in their cold room temporarily (contact: Dr. Lindgren). 
Eventually, we got a freezer to keep in the 480 lab. Between the VMS and 480 freezers though, we still only had space to store about half of what we got. 
This extra material was given away to the CTRL-H maker space, the OSU robotics lab, and the WSU rocket team. 
The vacuum bagging material found a semi-permanent home in the capstone lab, but even that isn't "supposed" to be there. (This situation is still developing.)

The lesson here is that you should only accept donations that you can use. It may feel like you're being rude to refuse a donation, but you can end up causing lots of problems for yourself. 

### Machine Sciences

In this same vein, we got a lot of aluminum and machine time donated by Machine Sciences (contact: [Dani Yeager](dani.yeager@machinesciences.com) and [Brian McCabe](brian.mccabe@machinesciences.com)). They provided the coupling rings and fin frames for the project. 

Their willingness to donate is essentially based on Brian's excitement about the project. Keep this in mind if you plan on asking for donations from them. You'll want to emphasize the novelty and spaciness of the project.

The other really important thing about Machine Sciences is the lead times. They are a high-end commercial job shop. Their customer's orders come first. If they're machining parts for you, get your order in as soon as you can, _**while still doing a good job on the design and double-checking things with your team mates and PSAS**_.
You don't want to find yourself waiting for a solid two months of other jobs to finish, like we did.

## Parts

This was a weird project for design. That is to say, there was disturbingly little "real" engineering design.
There were a lot of "OMG, this needs to be done yesterday" type tasks. So, even when it would have been appropriate to spend a month or more on the design of a part, we ended up going with a "it's probably fine" method of design.

The vast majority of the design was done using OpenRocket (OR). It's strictly an amateur tool, but still gives pretty accurate results. 
Our other main tools were OpenFOAM, Abaqus, and first-principles calculations.

For many of our first-order approximations, we simply used the OR model of Launch 12 (L12), since it was known to be very accurate. Once we had a reasonable guess as to what L13 would look like (including the nose and fin planform), we did calculations based on that, refining the model as we went.

### Nose

Initially, we were very worried about the design of the nose. The drag on the rocket dissipates kilowatts of power. 
Assuming the vast majority of it got dissipated as wave drag on the tip, we might expect the tip to reach hundreds of degrees C, depending on the size of the aluminum tip. We were worried that the tip might go beyond the operating range of the epoxy in the CF.

We got to this by taking the output of the OR simulation of L12, and summing the work done by the drag at each time step. Assuming all of that work went into the nose tip and that it was evenly distributed throughout the aluminum tip, we could calculate the temperature of a tip of a given size. 
Of course, these assumptions were totally heinous, but they gave an upper bound for how hot the tip might get.

After that, we tried to get a more accurate estimate of the tip temperature by using analytical expressions for the wave drag and skin drag, and relating them to the ratio of how much energy is dissipated by each. 
Unfortunately, the derivation of those was a bit beyond the scope of the project. The ones we found were either wrong or we weren't using them properly, because they disagreed wildly with the OR model. 

Next, we tried CFD. (It was probably silly jumping to this, but meh.) The OpenFOAM model predicted a maximum air temperature of only 175 degrees F. To back this up, [Peter](peter@mccloudaero.com), from NASA, got a similar result.
This meant that the tip size didn't matter much, as far as temperature. It just needed to be practical.

So, having the major dimensions (Based on the literature we found a 1:5 aspect von Karman nose was a very reasonable choice.) of the nose cone, we went about making CAD and talking to Machine Sciences about getting a mandrel machined. 
We decided to use a similar design as the modules, using a male mandrel to layup a CF-nomex-CF sandwich. 
Our reasoning behind this was that the sandwich was sort of a known technology that we already had practice with.

This presented a few challenges. 
First, Machine Sciences had trouble just machining it. (In fact, they eventually concluded that they couldn't machine it without buying some really expensive add-on to one of their machines.) Second, it was a *huge* part. Unless Machine Sciences could hog out the core of it -- they could only do about half -- it would take 3 people just to lift. 

Ultimately, they couldn't make the part. Even if they could, it would have been done after the launch date. Unfortunately, this became apparent after we had done all the CAD for the associated parts and been going under the assumption that we would have that tooling.

So, we had to figure out a new strategy for making the nose. 

We decided on a much more common method for forming noses: molding. This had the very attractive quality that many other amateur rocketeers built their nose cones by forming sections of the nose with a female mold and then joining them together. 
The main difference between our design and most others was that we were using high temperature prepreg CF, while most other groups used room-temperature cure epoxy painted onto raw CF.

We went back and forth between making a positive plug in the shape of the nose versus just making a female mold directly.
With the plug, we would machine the shape of one side of the nose, then mold FG on that and use the resulting FG mold to make the half-section of the nose. 
With the direct female mold, we would machine the negative shape of the half-section and then layup the CF on that directly.
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

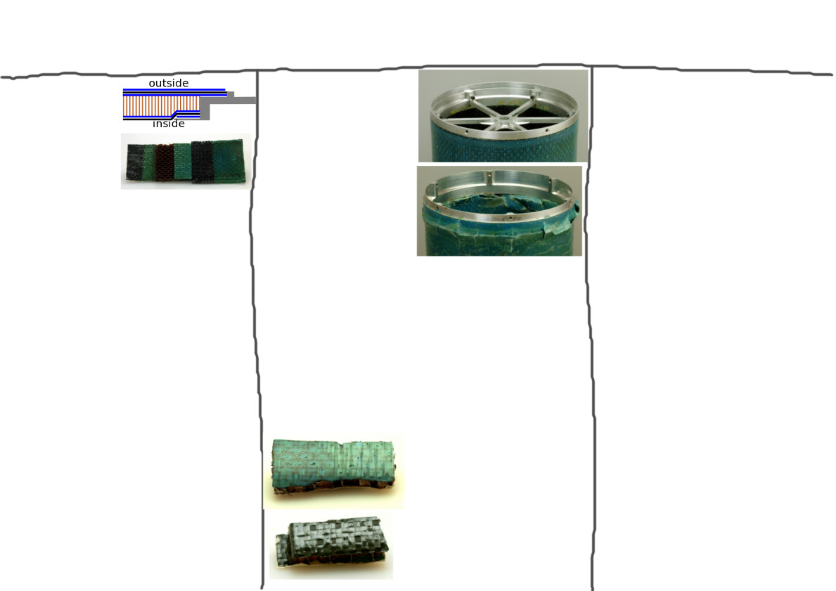
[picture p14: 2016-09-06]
doc/poster/layout/posterLayout.jpg

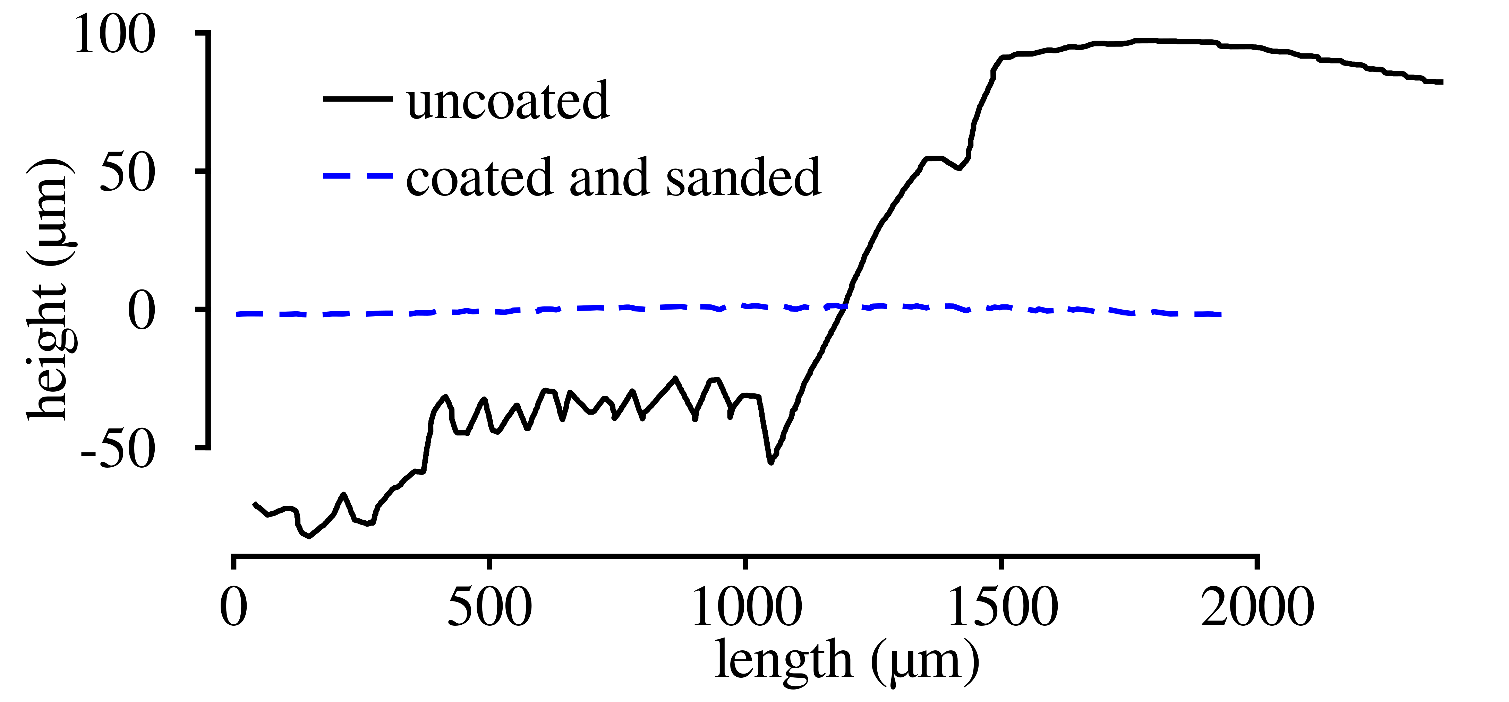
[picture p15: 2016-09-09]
doc/poster/roughness.png

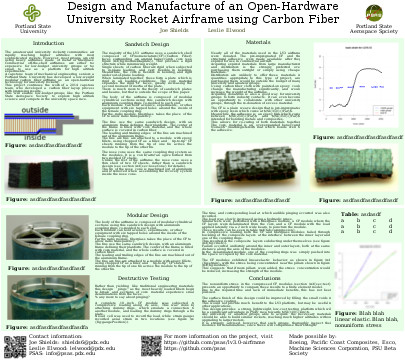
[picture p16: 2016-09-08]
doc/poster/layout/posterLayout_45x40in.jpg

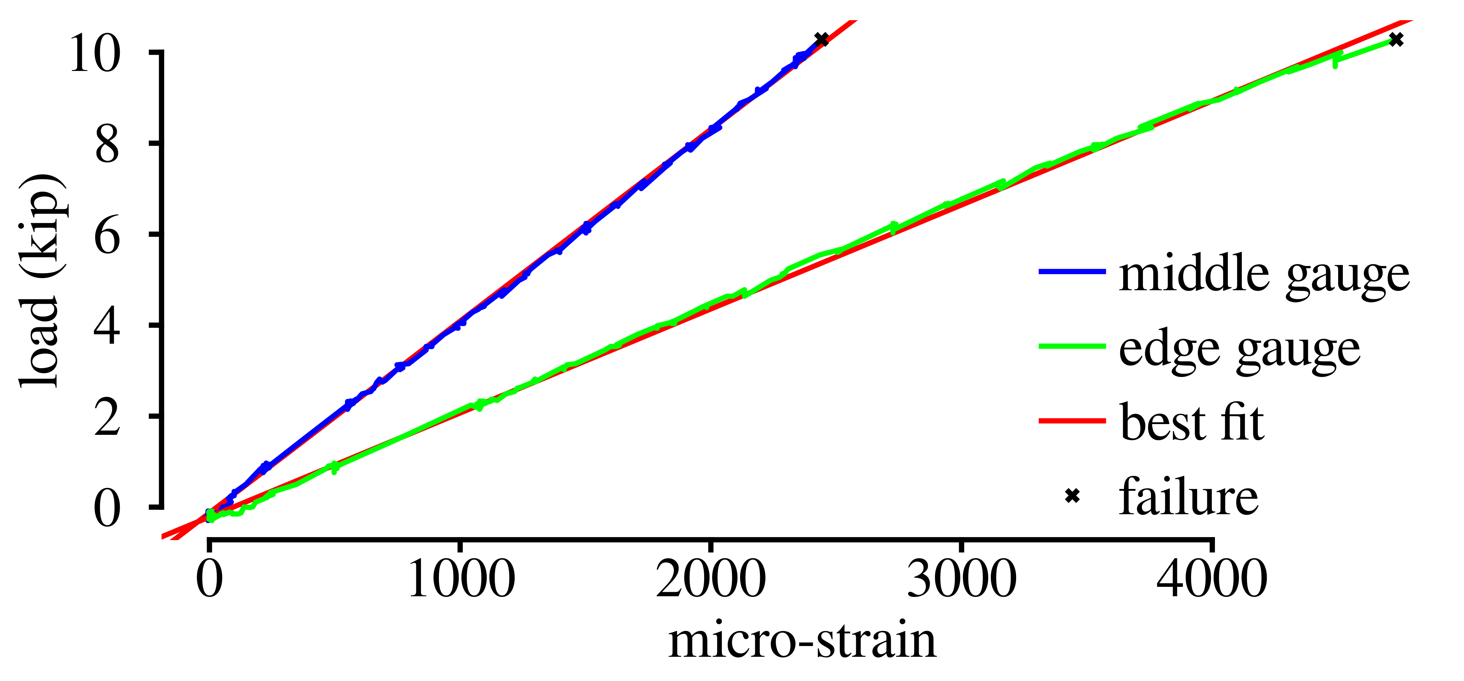
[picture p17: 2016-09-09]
doc/poster/strain.png

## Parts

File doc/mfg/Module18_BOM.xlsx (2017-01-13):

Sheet: Standard module BOM
Item # | Item | Part # | Qty | Source | Cost/Unit | Description | Other Sources | Link
 | Standard Module BOM
1 | Meltbond 1515-3M, 20''x16.85'' | 1515-3M | 1 | Pacific Coast Composites | Donation | Inner layer adhesive film |  | http://solutions.3m.com/wps/portal/3M/en_US/Aerospace/Aircraft/Prod_Info/Prod_Catalog/
2 | Meltbond 1515-3M, 22''x17.65'' | 1515-3M | 2 | Pacific Coast Composites | Donation | Outter layer adhesive film |  | http://solutions.3m.com/wps/portal/3M/en_US/Aerospace/Aircraft/Prod_Info/Prod_Catalog/
3 | Meltbond 1515-3M, 21''x.35'' | 1515-3M | 2 | Pacific Coast Composites | Donation | Coupling ring adhesive film |  | http://solutions.3m.com/wps/portal/3M/en_US/Aerospace/Aircraft/Prod_Info/Prod_Catalog/
4 | CYCOM 934 EPOXY PREPREG, 20''x16.85'' | BMS 8-297 3K-70-PW TY4 CL2 | 1 | Pacific Coast Composites | Donation | Inner prepreg carbon fiber ply (preferrably 5 Harness, can be plain weave) |  | http://www.cemselectorguide.com/pdf/CYCOM_934_032012.pdf
5 | CYCOM 934 EPOXY PREPREG , 22''x17.56'' | BMS 8-297 3K-70-PW TY4 CL3 | 1 | Pacific Coast Composites | Donation | Outter prepreg carbon fiber ply (preferrably 5 Harness, can be plain weave) |  | http://www.cemselectorguide.com/pdf/CYCOM_934_032012.pdf
6 | Female Mating Rings | N/A | 1 | Machine sicence | Donation | Aluminum
7 | Male Mating Rings | N/A | 1 | Machine sicence | Donation | Aluminum
8 | Honeycomb Core | N/A | 1 | Pacific Coast Composites | Donation | 1lb density,21.25''x16.94''x.25'' |  | http://www.hexcel.com/resources/honeycomb-data-sheets
9 | Assemble Screws | 93085A105 | 6 | Tacoma Screw | $8.01/100 | #4 40 100 deg countersunk screws 3/16 length | Mcmaster Carr, Fastenal | http://www.mcmaster.com/#100-degree-flat-head-screws/=sal1lj
 | Layup Tools
10 | Layup Mandrel | N/A | 1 | Machined by Arrow | $350.00 | 27''x6''OD
11 | Dummy Layup Rings | N/A | 2 | Machined in house | $180.00 | Aluminum
12 | Mandrel Screws | 93085A105 | 6 | Tacoma Screw | $8.01/100 | #4 40 100 deg countersunk screws 3/16 length | Mcmaster Carr, Fastenal | http://www.mcmaster.com/#100-degree-flat-head-screws/=sal1lj
13 | Perforated Shrink Tape | V-24A | 900" | ACP Composites | $21.63/roll | 1" Shrink Tape - Perforated/Release Coated | Pacific Coast Composites | http://www.acpsales.com/home.html
14 | Flash Tape (or kapton tape) | NA | 10" | ACP Composites | 20.01/roll | 1" Flash Breaker Tape 72 yd Roll | Pacific Coast Composites
15 | Cutout Templates | NA | 4 | Laser cut in house | NA | See description in steps 1 through 6 instruction | Tap Plastics
16 | Heat Gun | 96289 | 1 | Harbor Freight | $14.95 | 1500 Watt Dual Temperature Heat Gun | Home Depot, Mcmaster carr | http://www.harborfreight.com/1500-watt-dual-temperature-heat-gun-572-1112-96289.html
17 | Tongue Depressors | NA | 2 | Fred Meyer | 5/bag | Wood | Home Depot, Mcmaster carr
 | Powderless Nitrile Gloves |  | ~30 | Ace Hardware | ~$5/box | keep skin oil in and carcinogens out | most stores
 | release film, 20''x16.35'' |  | 1 | ??? | Donation | inner release
 | release film, 2' x 20" |  | 1 | ??? | Donation | outer release
 | vacuum bag breather, 4' x 2' |  | 1 | Boeing | Donation | breather layer
 | vacuum bag sealing tape, 16' |  | 1 | ??? | Donation | goop tape
 | vacuum bag sheet, 4' x 2' |  | 2 | Boeing | Donation | inner/outer vac bags
 | Treatment Chemicals
18 | ORCA Clean | 252202 | .25 cups | Fiberlay | $94.21/gal | Mold cleaner | Acetone or similar
19 | 3M Surface Pre-Treatment | AC-130 | 25 mL | Pacific Coast Composites | Donation | Aluminum surface treatment
20 | ORCA Seal | 252203 | .25 cups | Fiberlay | $128..88/gal | Mold sealer | Frekote 700 or similar

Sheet: Sheet1
Item | Part No. (If applicable) | Qty. | Source | Cost/Unit | Description | Other Sources | Link
Parts
Adhesive film | Old glue and New glue | 2 | Pacific Coast Composites |  | 18" x 18" and 18" x 18"
Pre-preg carbon fiber | 5 Harness Prepreg CF | 2 | Pacific Coast Composites
Aluminum mating rings | MCR and FCR | 2 |  |  | MCR and FCR
Honeycomb core | .25" Nomex core 1lb density | 1 | Pacific Coast Composites |  | 18 x 18
Fasteners |  | 20 | Tacoma Screw |  | #4 40 100 deg countersunk screws 3/16 length | Mcmaster Carr, Fastenal
Tools
Layup table | LT-001 |  | Capstone Built
Curing oven | CO-002 |  | Capstone Built
Freezer | CF-003 |  | Sung Yi |  |  | Craigslist
Tools - Consumables
Razor knife |  | 1 | Tacoma Screw | $2.50 |  | Home Depot, Mcmaster carr
Scissors |  | 1 | Tacoma Screw | $2.00 |  | Home Depot, Mcmaster carr
Layup mandrel |  | 1 | Machined by Arrow | $350.00 |  | Aluminum from EMJ
Mandrel holder stand |  | 2 | 3D Printed in house
Perforated shrink tape |  | 900" | ACP Composites |  |  | Pacific Coast Composites | http://www.acpsales.com/home.html
Flash tape |  | 10" | ACP Composites |  |  | Pacific Coast Composites
Dummy layup ring |  | 2 | Machined in house | $180.00 | Stock from Speedy Metals
Mandrel fasteners |  | 6 | Tacoma Screw | $0.50 | #4 40 100 deg countersunk screws 3/16 length | Mcmaster Carr, Fastenal
Mandrel curing stand |  | 2 | Aluminum made in house |  | Metal from Scrap
Cutout templates |  | 4 | Laser cut in house |  | Steps 1 through 6 | Tap Plastics
Shop towels |  | 2' | Tacoma Screw |  | Blue automotive towels work best | Home Depot, Mcmaster carr
Acetone |  | .25 cups | Fiberlay |  | ORCA Clean is what we use | Home Depot, Mcmaster carr
3M Alum. surface treatment |  | 25 mL | Pacific Coast Composites
Alum. treatment brush applicator |  | 1 | Tacoma Screw |  | Any standard brush works | Home Depot, Mcmaster carr
Gloves
M - Box |  | 1 | Winks |  |  | Home Depot, Mcmaster carr
XL - Box |  | 1 | Winks |  |  | Home Depot, Mcmaster carr
ORCA Hybrid Mold Release |  | .25 cups | Fiberlay
Sandpaper |  | 10 in^2 | Homedepot |  | 320 and 600 grit
Sharpie marker |  | 2 | Safeway |  | Fine Point | Home Depot, Mcmaster carr
Tongue depressors |  | 2 | Fred Meyer |  | Standard wood
Heat gun |  | 1 | Rob Melchione |  |  | Home Depot, Mcmaster carr

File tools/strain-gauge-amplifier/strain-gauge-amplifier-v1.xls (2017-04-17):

Qty | Parts | Value | Device | Package | Description
1 | C1 | 1uF | C-EU0805-C-NOSILK | 0805-C-NOSILK | CAPACITOR, European symbol
3 | C2,C3,C4,C5 | 100n | C-EU0805-C-NOSILK | 0805-C-NOSILK | CAPACITOR, European symbol
1 | IC2 | INA125U | INA125U | SO16-1 | Instrumentation Amplifier
4 | JP1,JP2,JP3,JP5 | 2pin 0.2" Eurutomerinal | M025MM | SCREWTERMINAL-5MM-2 | Header 2
1 | LED1 | 2.1V/20mA | LED0603 | LED-0603 | LEDs
1 | Q1 | PMV45EN | PMV45EN | SOT23
2 | R1, R3 | 120 | R-US_0805-C-NOSILK | 0805-C-NOSILK | RESISTOR, American symbol
2 | R2A, R8 | 100 | R-US_0805-C-NOSILK | 0805-C-NOSILK | RESISTOR, American symbol
1 | R2B | 50ohm/20turn | PV36W500C01B00 | TRIMPOT-5MM | Various small potentiometers for
2 | R4, R10 | 1k | R-US_0805-C-NOSILK | 0805-C-NOSILK | RESISTOR, American symbol
1 | R6 | NP (0) | R-US_0805-C-NOSILK | 0805-C-NOSILK | RESISTOR, American symbol
1 | R7 | NP (10k) | R-US_0805-C-NOSILK | 0805-C-NOSILK | RESISTOR, American symbol

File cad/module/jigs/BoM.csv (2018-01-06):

item | quantity | cost | description | notes | link
31 gauge collar | 1 | 3.22 | annular collar intended as a depth gauge for drilling |  | https://www.mcmaster.com/#8865a131/=1agiqq7
30 gauge collar | 1 | 3.45 | annular collar intended as a depth gauge for drilling |  | https://www.mcmaster.com/#8865a133/=1agjch6
43 gauge collar | 1 | 3.22 | annular collar intended as a depth gauge for drilling |  | https://www.mcmaster.com/#8865a114/=1agjcx9
1/2" dowell pin | 1 | 3.17 | indexes cradle mount plate |  | https://www.mcmaster.com/#98381a708/=1agj28q
1/8" dowell pin | 1 | 10.01 | indexes cradle mount plate | 100 pack | https://www.mcmaster.com/#98381a471/=1agj3c7
#8-32 set screw | 1 | 8.29 | retains collars | 10 pack | https://www.mcmaster.com/#91381a192/=1b08ei5

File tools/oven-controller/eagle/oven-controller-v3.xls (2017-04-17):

Qty | Parts | Value | Device | Package | Description | Digikey Part No
10 | C1-C10 | Cap, 100n 100V 10% X7R | C-EUC0603K (C-EU) | C0603K | CAPACITOR, European symbol
5 | C7,C11-C14 | Cap, 10n, 1%, X7R | C-EUC0603K (C-EU)
10 | JP1-JP10 | 2pin 0.1” Euroterminal
5 | LED1-LED5 | 2.1V/20mA RED | LED0603 | LED-0603 | LEDs
4 | Q1-Q4 | N-FET, 20V 0.9A | FDV305N | SOT23 | MOSFET N-CH 20V 0.9A SOT-23 | FDV305NCT-ND
4 | R1-R4,R6 | Resistor, 10k 1/10W 1% | R-US_0603-C-NOSILK (R-US_) | 0603-C-NOSILK | RESISTOR, American symbol
5 | R5,R7-R10 | Resistor, 1k, 1/10W, 1% | R-US_0603-C-NOSILK (R-US_) | 0603-C-NOSILK | RESISTOR, American symbol
5 | U2-U6 | MAX31855KASA+T | MAX31855KASA+T | SO-8 | IC CONV THERMOCOUPLE-DGTL 8SOIC | MAX31855KASA+-ND

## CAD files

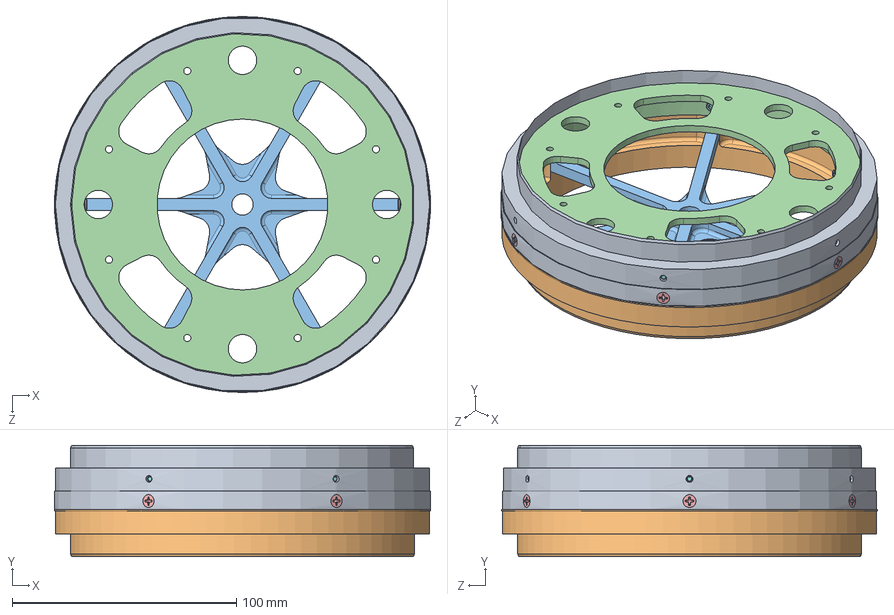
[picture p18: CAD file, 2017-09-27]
cad/couplingExample.SLDASM
167.6 x 49.7 x 167.6 mm
femaleRing
maleRing
spider
CradleInterfaceRing
4-40_3_16th_93085A105_18-8 SS 100 DEG FLAT HEAD PHIL MACHINE SCREW x 6
4-40_1_4th_92196A106_18-8 STAINLESS STEEL SOCKET HEAD CAP SCREW x 6
No4_98019A218_MIL SPEC. 300 SERIES SS FLAT WASHER x 6
4-40_3_8th_92196A108_18-8 STAINLESS STEEL SOCKET HEAD CAP SCREW x 6

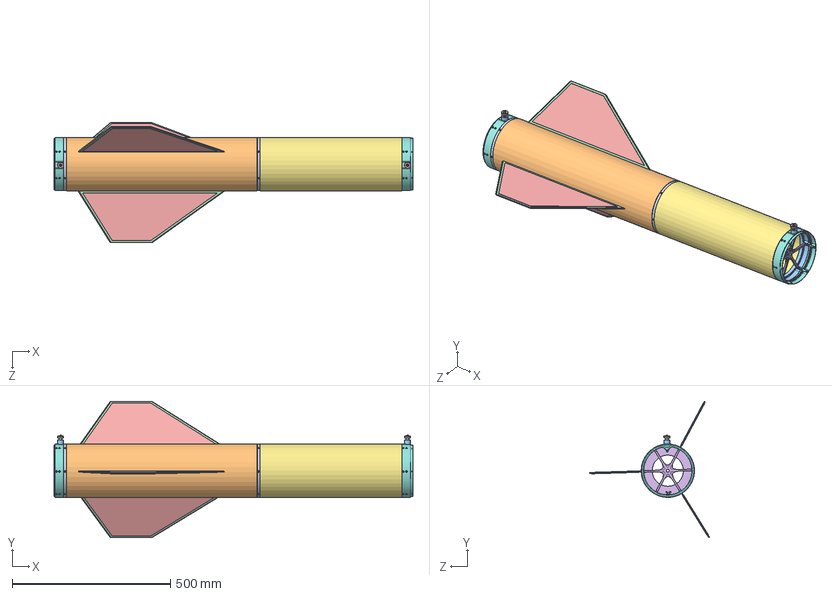
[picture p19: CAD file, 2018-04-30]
cad/finCan/finCan.SLDASM
1133.2 x 429.9 x 379.1 mm
femaleRing x 2
carbonSleeve24
maleRing x 2
LongFins_ALedge x 3
finShell x 6
spider
carbonSleeve18
buttonRing x 2
No10-24x2buttonHead_316_98164A458_TYPE 316 SS BUTTON-HEAD SOCKET CAP SCREW x 2
topRound x 2
bottomRound_forMidRing x 2
No10x0.375x0.25PTFEbushing_95136A110_PTFE UNTHREADED SPACER x 2
No10x0.75washer_90377A125_BLACK-OXIDE 18-8 STAINLESS STEEL FLAT WASHER x 2
motorMount

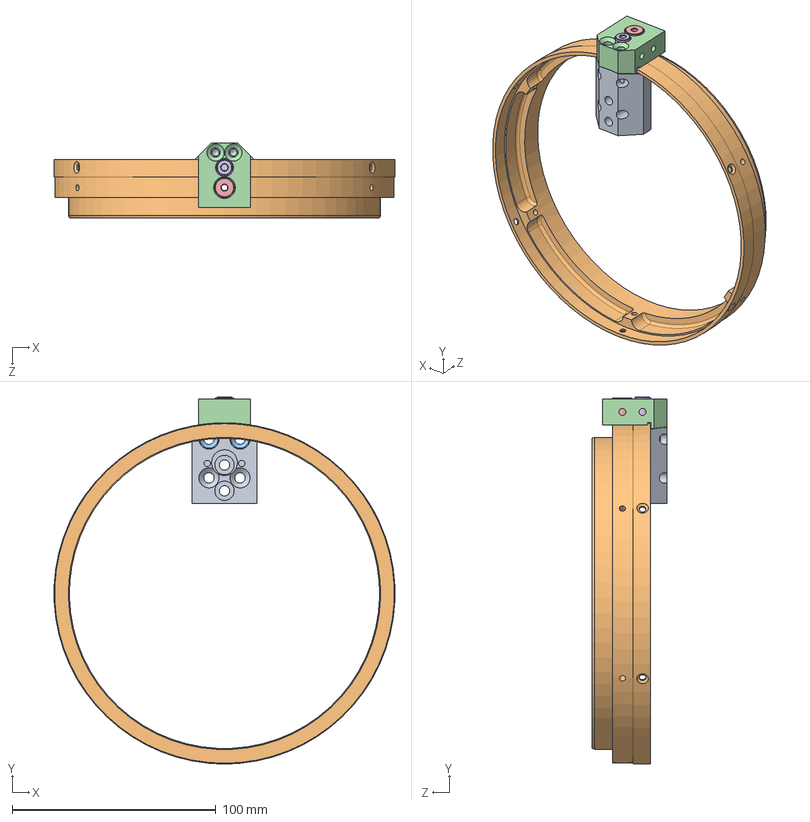
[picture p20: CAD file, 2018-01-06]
cad/module/jigs/femaleRingDriller.SLDASM
167.5 x 180.3 x 37.0 mm
basePlateFemale
femaleRing
pillarAligner x 2
holeSteadyFemale
31gaugeDrillCollar
30gaugeDrillCollar_narrow

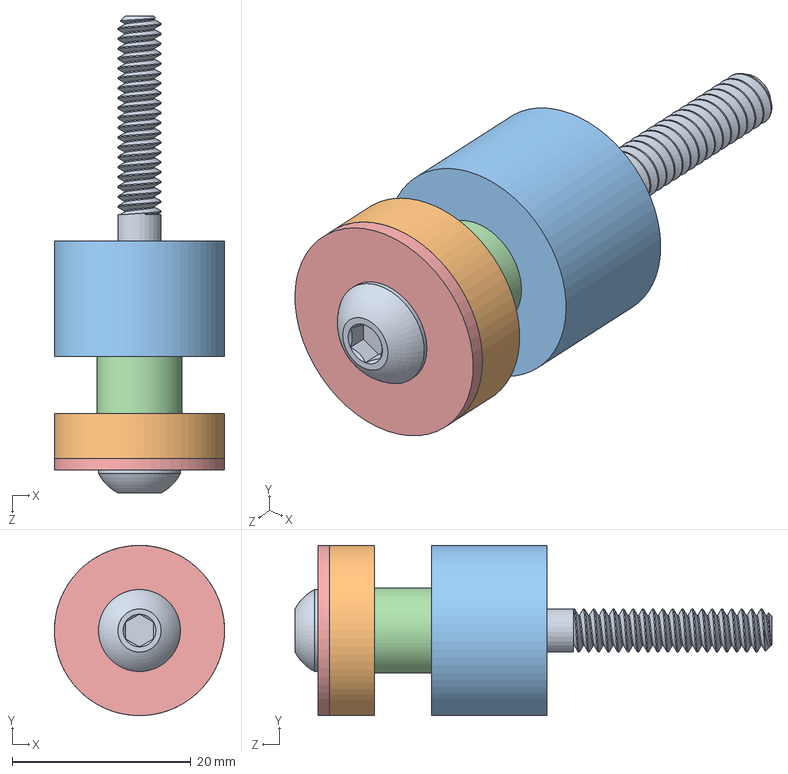
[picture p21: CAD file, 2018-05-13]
cad/railSled/button/button_forMid.SLDASM
19.0 x 19.1 x 53.4 mm
No10-24x2buttonHead_316_98164A458_TYPE 316 SS BUTTON-HEAD SOCKET CAP SCREW
topRound
bottomRound_forMidRing
No10x0.375x0.25PTFEbushing_95136A110_PTFE UNTHREADED SPACER
No10x0.75washer_90377A125_BLACK-OXIDE 18-8 STAINLESS STEEL FLAT WASHER

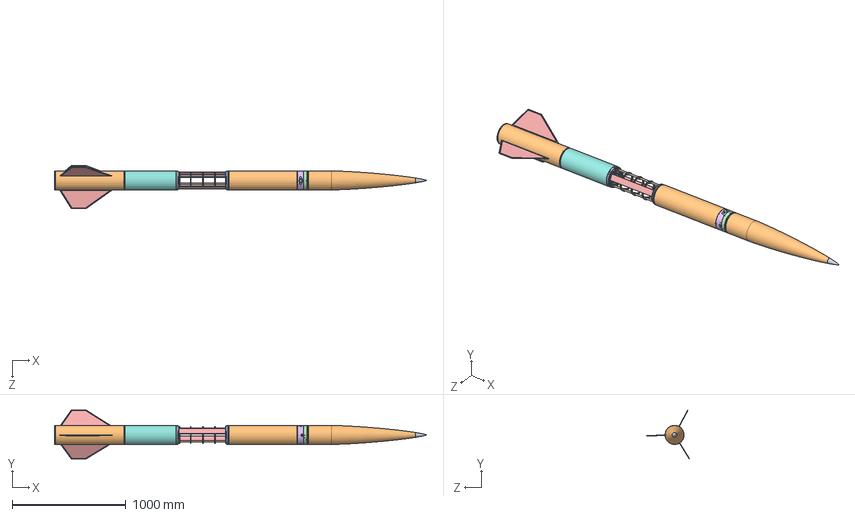
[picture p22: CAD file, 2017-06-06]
cad/LV3.SLDASM
3273.9 x 429.9 x 379.1 mm
femaleRing x 5
carbonSleeve24 x 2
maleRing x 4
LongFins_ALedge x 3
finShell x 6
spider
motorMount
von_karmon_nose_tip2
nosePlug2
NSRlower 2.0v3 flipped
NSRupperv3.0 Flipped
Nozzle carrying ring (3_4_15)
deLaval pitch yaw x 2
deLaval roll and pitch coupled nozzles x 2
CradleInterfaceRing x 2
CradleWiring x 2
CradleRibEnds x 2
CradleRibMid x 5
CradleSideWalls x 2
binding head screw_ai x 16

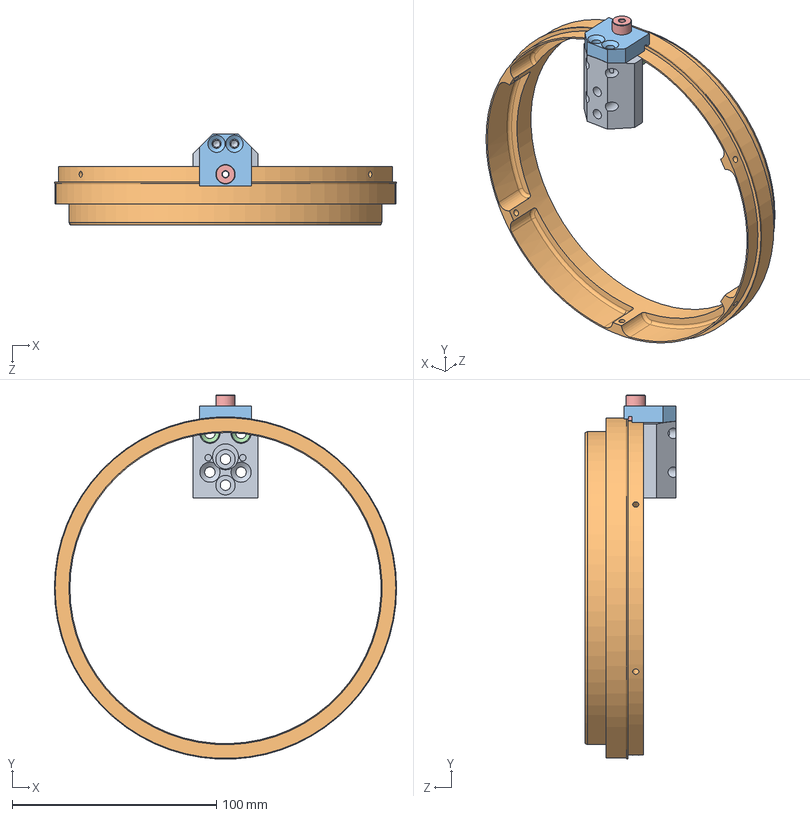
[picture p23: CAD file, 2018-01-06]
cad/module/jigs/maleRingDriller.SLDASM
167.6 x 178.3 x 44.5 mm
basePlateFemale
maleRing
holeSteadyMale
pillarAligner x 2
31gaugeDrillCollar

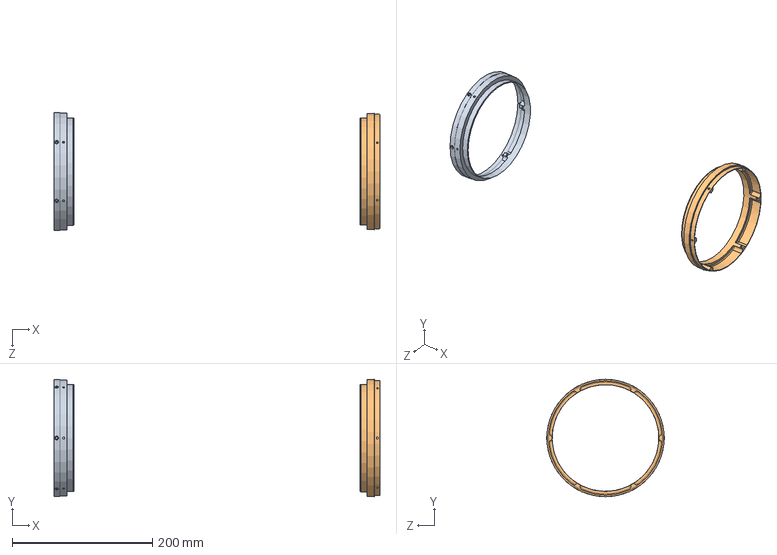
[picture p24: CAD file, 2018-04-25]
cad/module/Module18.SLDASM
464.8 x 167.6 x 167.6 mm
femaleRing
maleRing

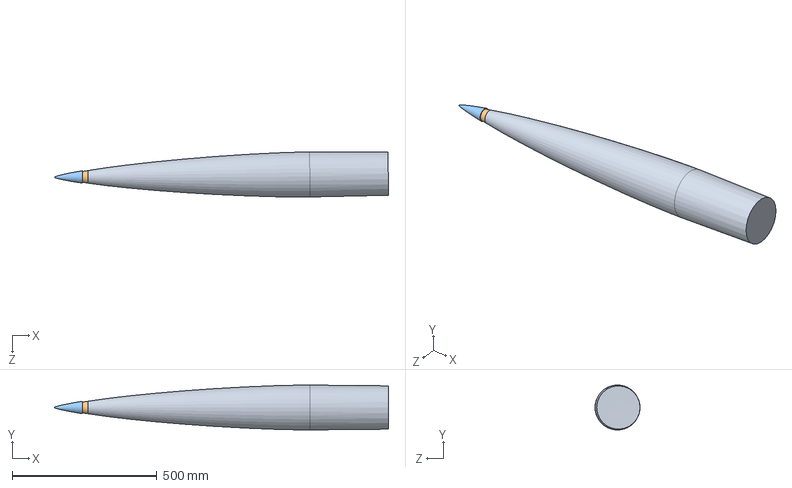
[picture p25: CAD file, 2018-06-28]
cad/nose/lv3.1-nose/LV3.1mandrel.SLDASM
1154.0 x 155.0 x 155.9 mm
updatenoseplugLV3.1
nosePlug2
von_karmon_nose_tip2

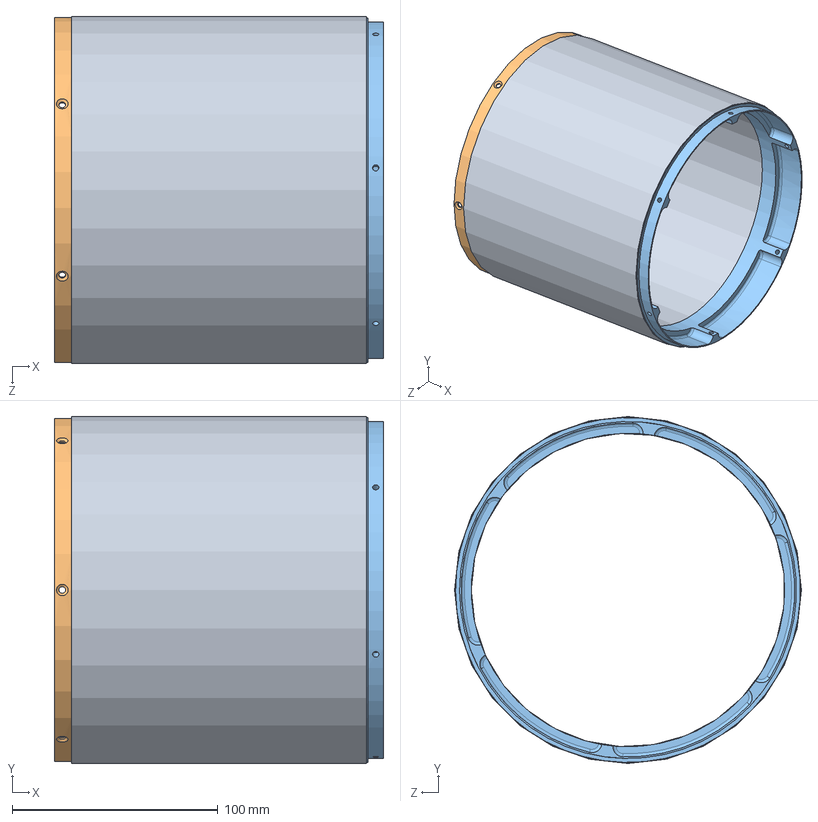
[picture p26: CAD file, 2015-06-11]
cad/radome/PSAS-LV3.0-Antenna_Module_Top_Asm.SLDASM
160.0 x 168.7 x 168.7 mm
Fiberglass antenna module Sleeve
FCR 6in 4_6_14 Final
MCR 6in 4_6_14 Final

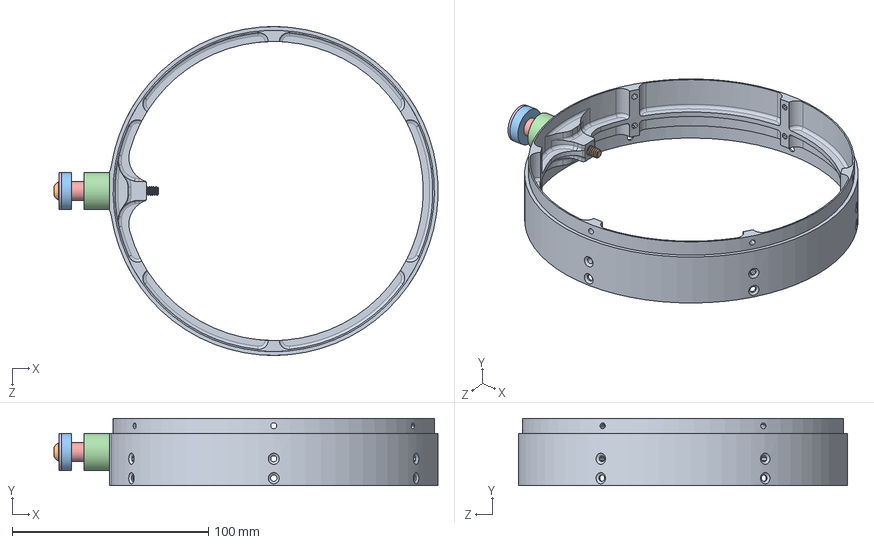
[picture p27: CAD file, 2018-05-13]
cad/railSled/button/hardPoint_mid.SLDASM
195.8 x 34.3 x 167.6 mm
buttonRing
No10-24x2buttonHead_316_98164A458_TYPE 316 SS BUTTON-HEAD SOCKET CAP SCREW
topRound
bottomRound_forMidRing
No10x0.375x0.25PTFEbushing_95136A110_PTFE UNTHREADED SPACER
No10x0.75washer_90377A125_BLACK-OXIDE 18-8 STAINLESS STEEL FLAT WASHER

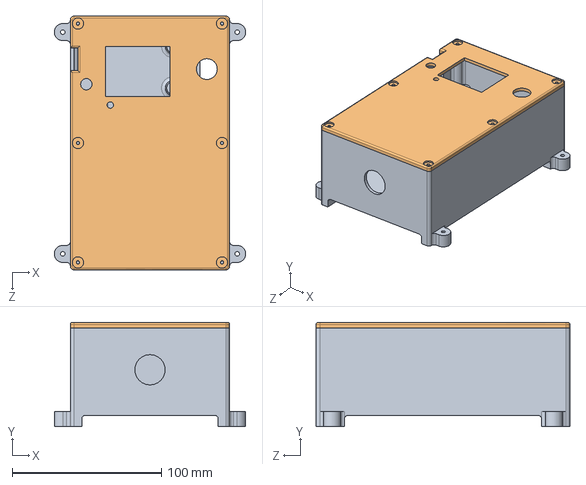
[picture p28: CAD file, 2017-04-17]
tools/oven-controller/Oven_Controller/Box/ASSY_Box.SLDASM
128.2 x 69.8 x 170.2 mm
Oven_box
Topcover_2

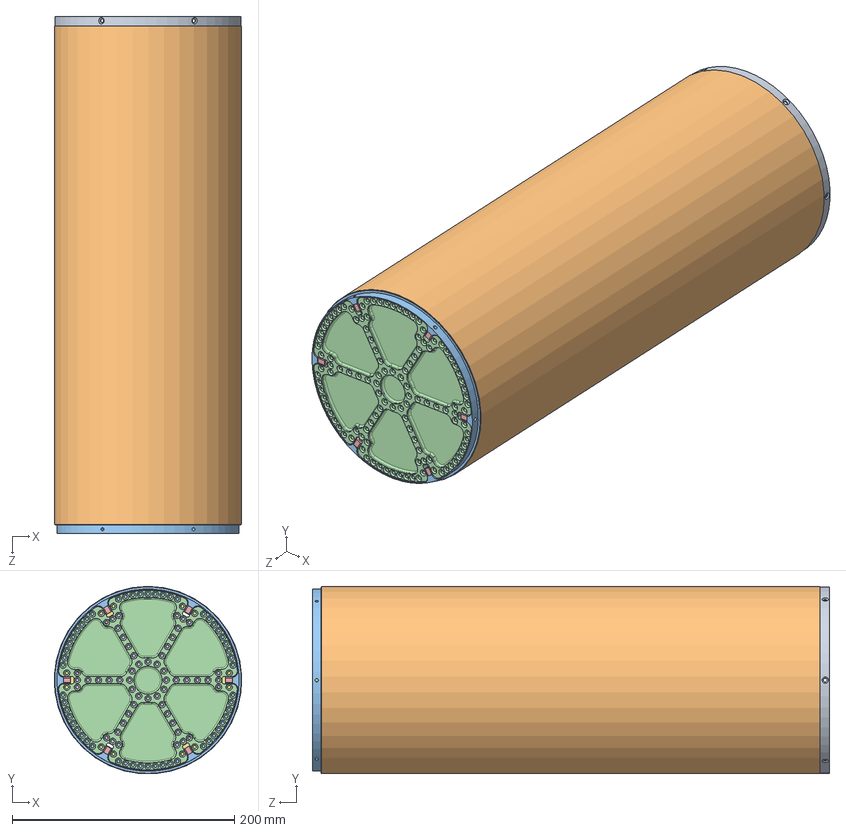
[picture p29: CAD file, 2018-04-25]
cad/cradle/cradleEnclosure.SLDASM
168.6 x 168.4 x 464.8 mm
femaleRing
carbonSleeve18
maleRing
bulkhead x 2
bulkheadBracket_straightHole x 12
bracketSpacer x 4
railCushion x 2
CradleRibMid x 5
CradleSideWalls x 4
longRib x 8

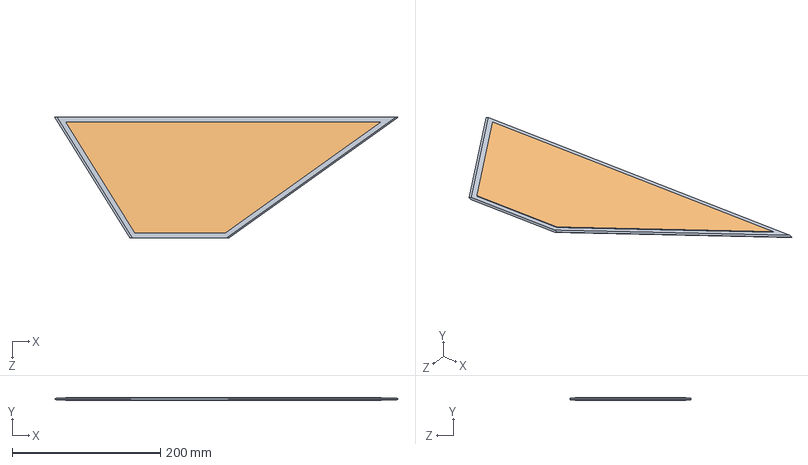
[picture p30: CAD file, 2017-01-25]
cad/finCan/LongFinFiles/LongFin.SLDASM
464.0 x 4.70 x 163.1 mm
LongFins_ALedge
finShell x 2

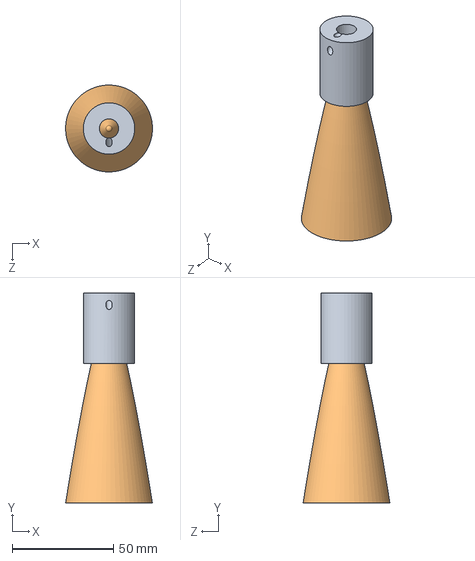
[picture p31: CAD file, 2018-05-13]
cad/nose/lv3.0-nose/tipSafetyExample.SLDASM
42.9 x 103.7 x 42.9 mm
tipSafety
von_karmon_nose_tip2

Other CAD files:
cad/railSled/button/hardPoint.SLDASM
tools/Composite_Table/Composite Table with Top Rack.SLDASM
cad/cradle/spacerBox.SLDASM
cad/module/jigs/fullJig.SLDASM
cad/COTS/4-40_1_4th_92196A106_18-8 STAINLESS STEEL SOCKET HEAD CAP SCREW.SLDPRT
cad/COTS/4-40_3_16th_93085A105_18-8 SS 100 DEG FLAT HEAD PHIL MACHINE SCREW.SLDPRT
cad/COTS/4-40_3_8th_92196A108_18-8 STAINLESS STEEL SOCKET HEAD CAP SCREW.SLDPRT
cad/COTS/4-40x0.25standoff_93505A430_ALUM MALE-FEM THRDED HEX STANDOFF.SLDPRT
cad/COTS/No4_98019A218_MIL SPEC. 300 SERIES SS FLAT WASHER.SLDPRT
cad/CubeSatAirframeMount/Cradle_lid_attachment_II.SLDDRW
cad/CubeSatAirframeMount/Cradle_lid_attachment_II.SLDPRT
cad/CubeSatAirframeMount/MasterCAM/Cradle_lid_attachment_II_V2.IGS
cad/Sanding Lathe.dwg
cad/ballast/ballastPlate.SLDDRW
cad/ballast/ballastPlate.SLDPRT
cad/couplingExample.SLDDRW
cad/cradle/CradleRibMid.SLDPRT
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

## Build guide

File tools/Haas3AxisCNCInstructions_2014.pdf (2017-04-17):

# HAAS 3-AXIS CNC

# OPERATING INSTRUCTIONS

Jack Slocum
Sam Arnold
Barett Strecker
Robert Melchione

5/28/2014

## TABLE OF CONTENTS

## CONTROL PANEL OVERVIEW

General organization:

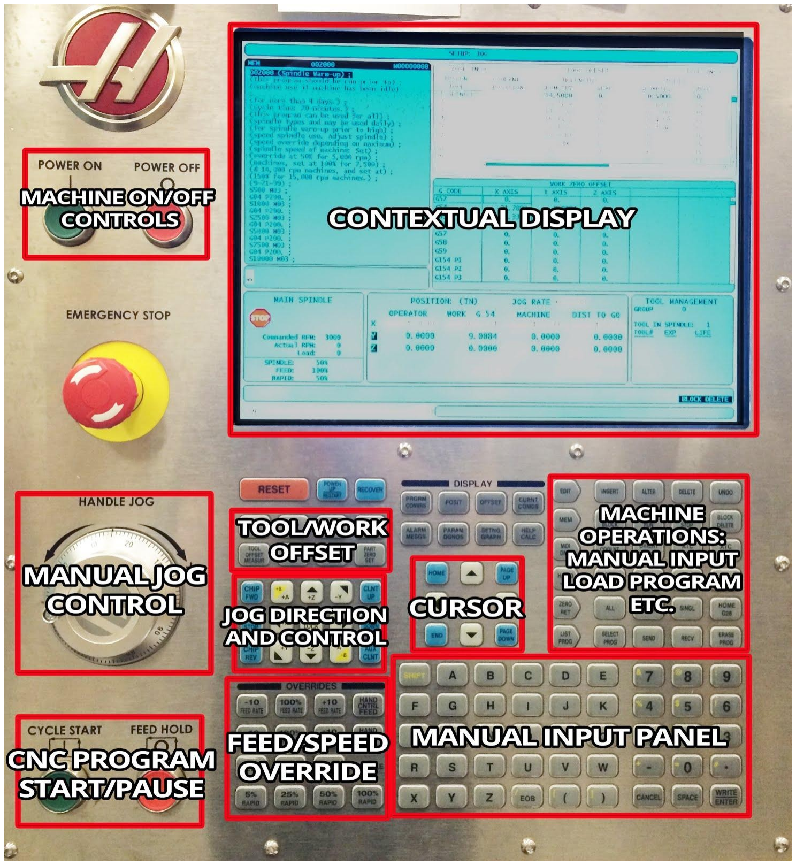
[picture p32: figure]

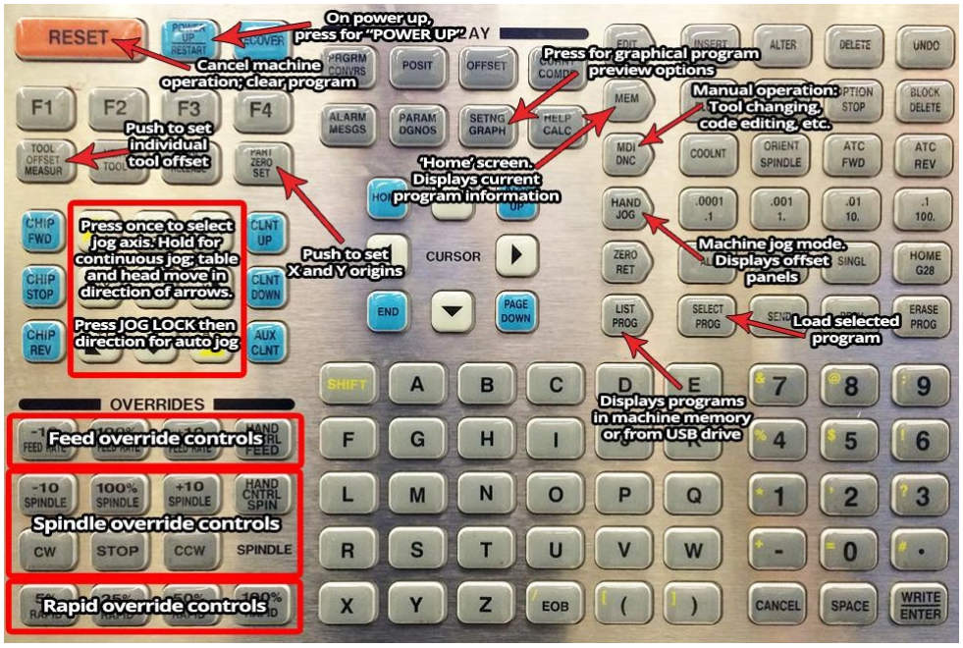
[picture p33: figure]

Detail view of common operations:

## MACHINE STARTUP INSTRUCTIONS

1. Start up machine following the prompts
a. Push the POWER ON button
b. Follow the prompts in the yellow blinking box on the left side:
i. EMERGENCY STOP on and off
ii. Close door (make sure the vice handle has been removed or it will crash into the door)
iii. | Push RESET
iv. | Push POWER UP
1. Wait until final beep
2. Run spindle warm up program program number 002000
a. Push LIST PROGRAM
b. Push ENTER to open machine memory tab
c. Scroll to the 002000 program, so it is highlighted
d. Push SELECT PROGRAM, not ENTER
e. Press MEM and look at the program in the memory panel to verify that program 002000 is loaded
f. Use Spindle Override to decrease spindle to 50%. This is necessary based on the max. RPM of the machine, which is 5000 RPM.
g. Cycle start
i. This program takes 20 minutes, and will incrementally increase the spindle speed up to 5000 RPM
3. Turn the machine light on. The button is located on the side of the control box, indicated by a light symbol

## PROGRAM PREPARATION

4. Open your part in Solidworks
5. Create coordinate system that will allow you to zero X, Y, and Z coordinates once your stock is in the machine.

a. Sketch a location you could measure on your stock

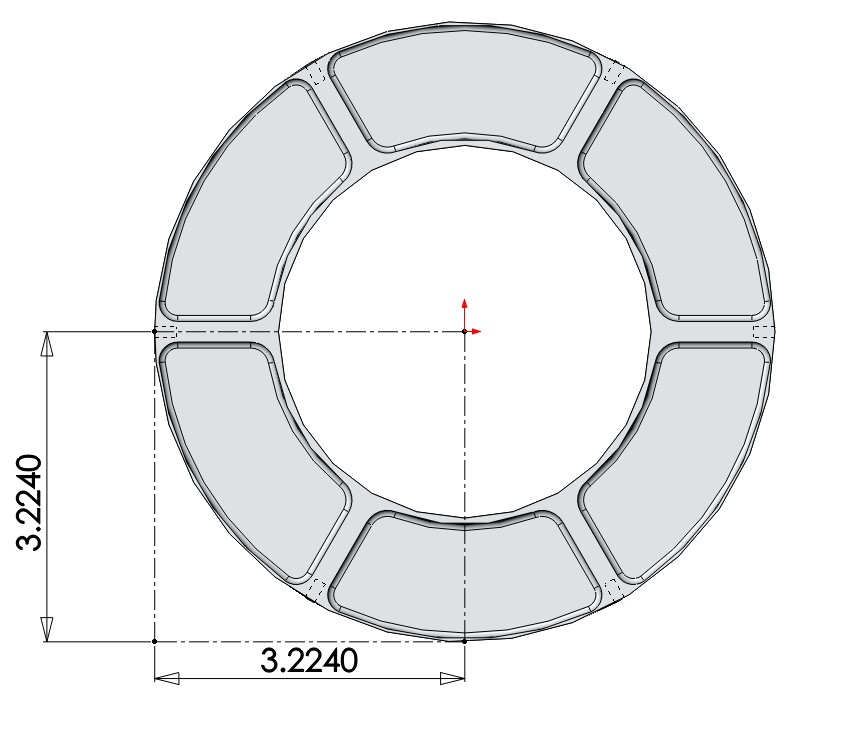
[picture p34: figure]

b. Create coordinate system, where Z is out of the screen toward you, X is to your right, and Y is up

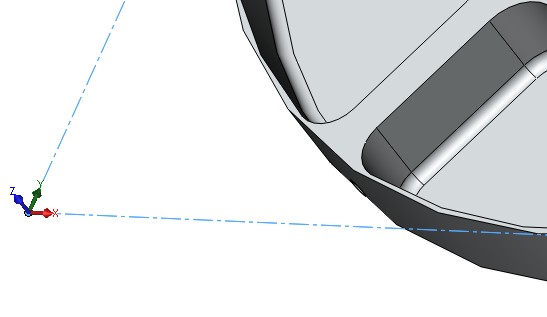
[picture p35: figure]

c.

d.

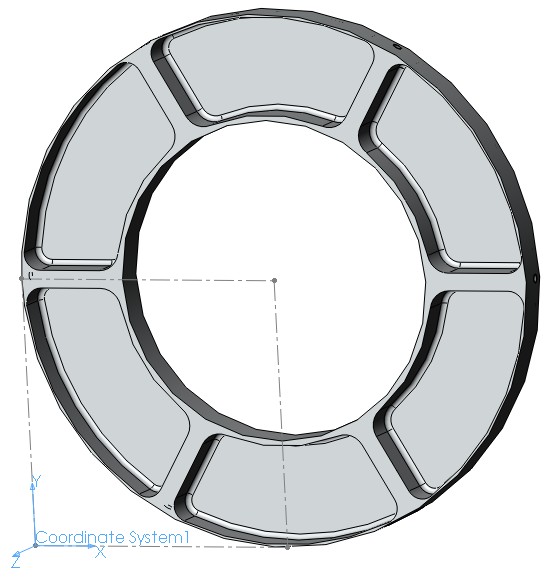
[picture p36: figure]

e. Save as IGES file type, and before clicking OK, click Options from the dropdown at the bottom of the window, set your output coordinate system to the one you just created

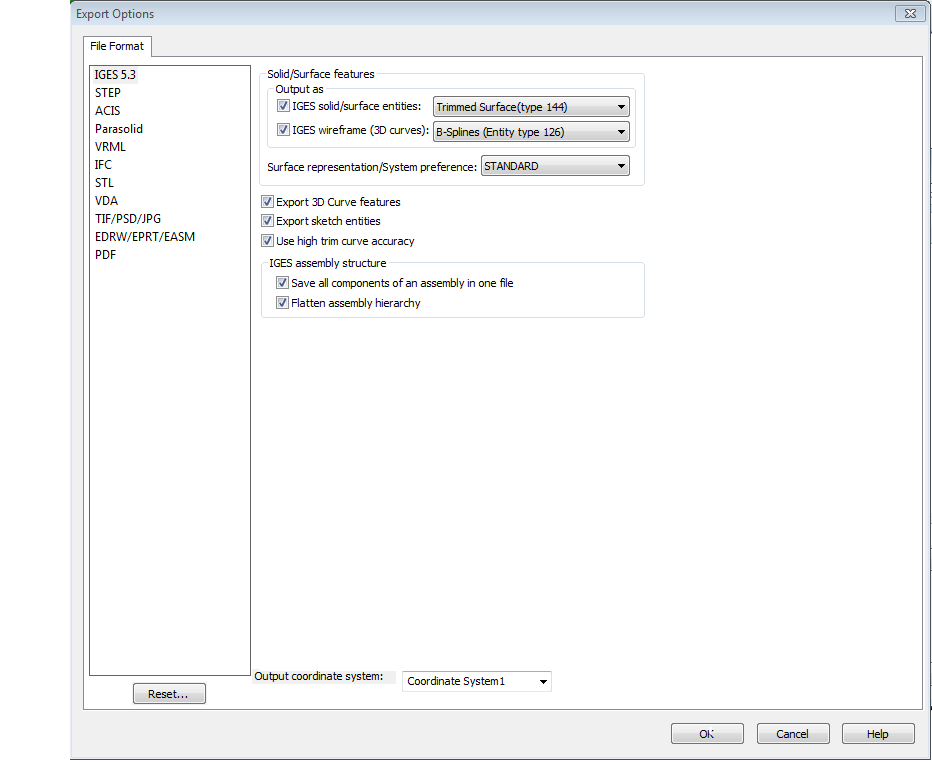
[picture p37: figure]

f.

## MASTERCAM PROGRAMMING

6. Open MasterCAM x7
7. Open your IGES part a. Your part should pop up facing you the way you intend to machine it

b.

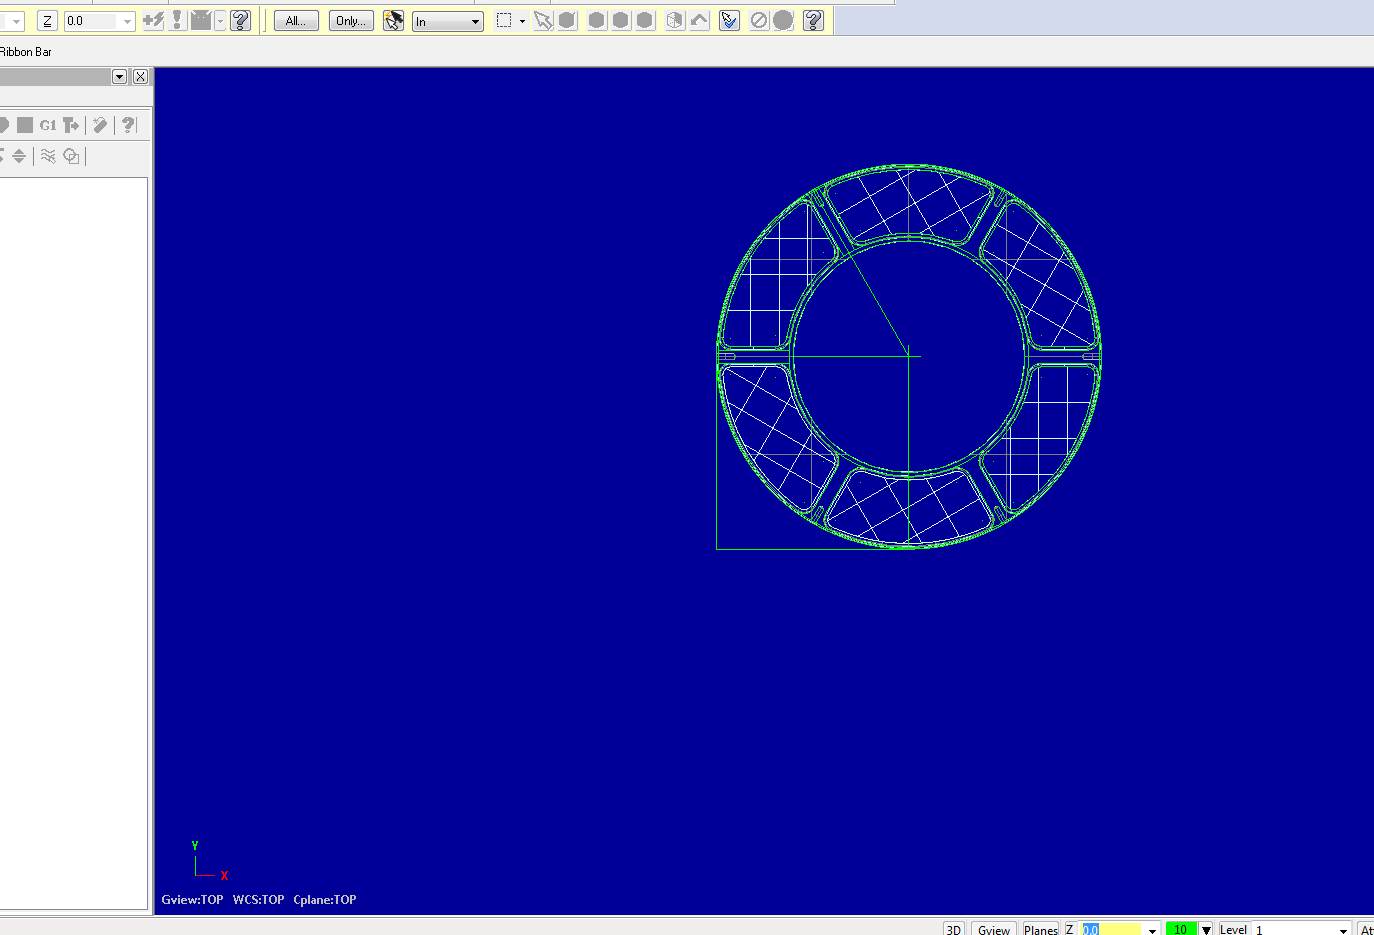
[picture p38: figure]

c. Select shaded, outlined icon to display part surfaces and outlines d.

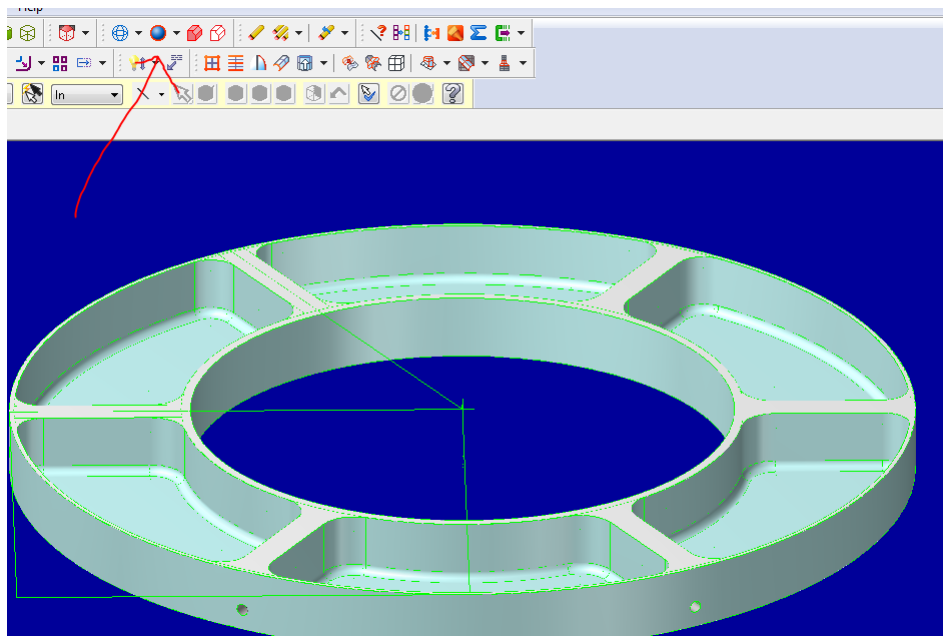
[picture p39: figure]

8. Click Machine Type > Mill > Manage List* (*only necessary if the Haas 3-axis is not already listed)

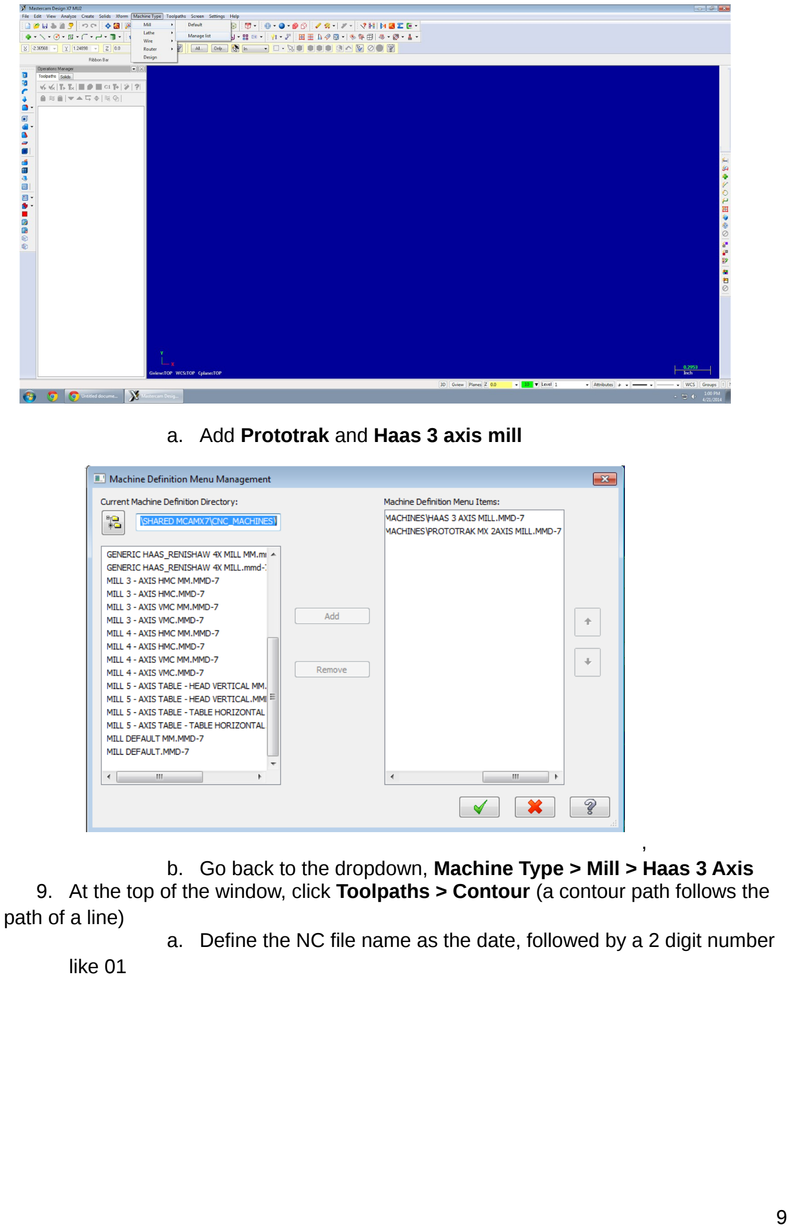
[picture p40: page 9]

a. Add Prototrak and Haas 3 axis mill

,
b. Go back to the dropdown, Machine Type > Mill > Haas 3 Axis
9. At the top of the window, click Toolpaths > Contour (a contour path follows the path of a line)
a. Define the NC file name as the date, followed by a 2 digit number like 01

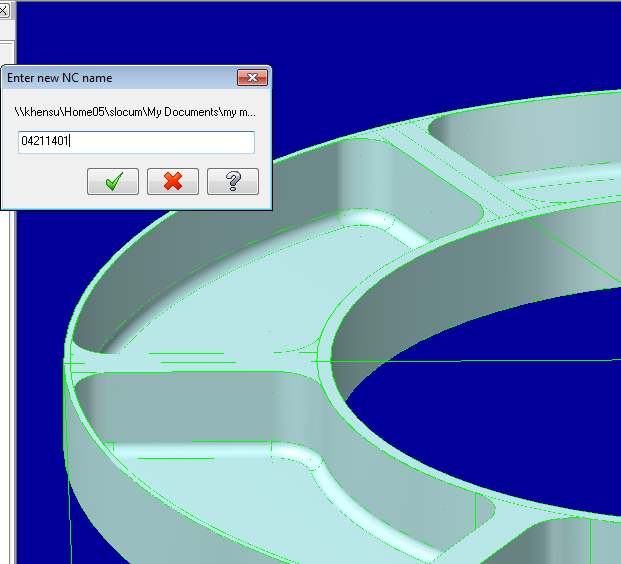
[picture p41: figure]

b. Select the contour lines you want to cut on. These lines can often be difficult to see. The red arrow is where your tool will finish its path, the green arrow is where it will begin. In general, you want to green and red arrows to end up on top of each other for a closed path. Click the Green Checkmark.
c. In the subsequent toolpaths window, click the Tool item in the left column, then click Select library tool, and find/select the tool you plan to use. You might have to uncheck “filter active.”

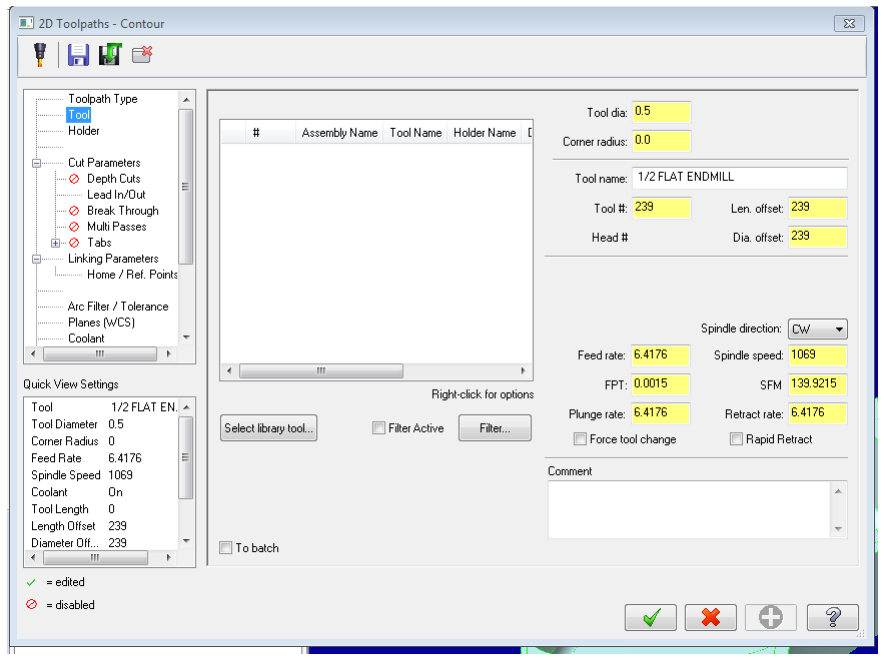
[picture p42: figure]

d. On the Haas, it is critical that the Tool #, Head #, Len. offset and Dia. offset are the same number. This number should match the tool’s position number indicated on the Haas tool carousel. This is how the machine knows what the tool geometry is. General feeds and speeds: aluminum, .5” diameter tool > 2200 rpm, 6 feed, 3 plunge. Smaller cutters generally need faster RPM and slower feed. Harder materials generally need slower RPM and slower feed.
e. Select Linking Parameters from the options tree on the left. The depth is the final depth of the cutter. Make sure each parameter is Absolute.

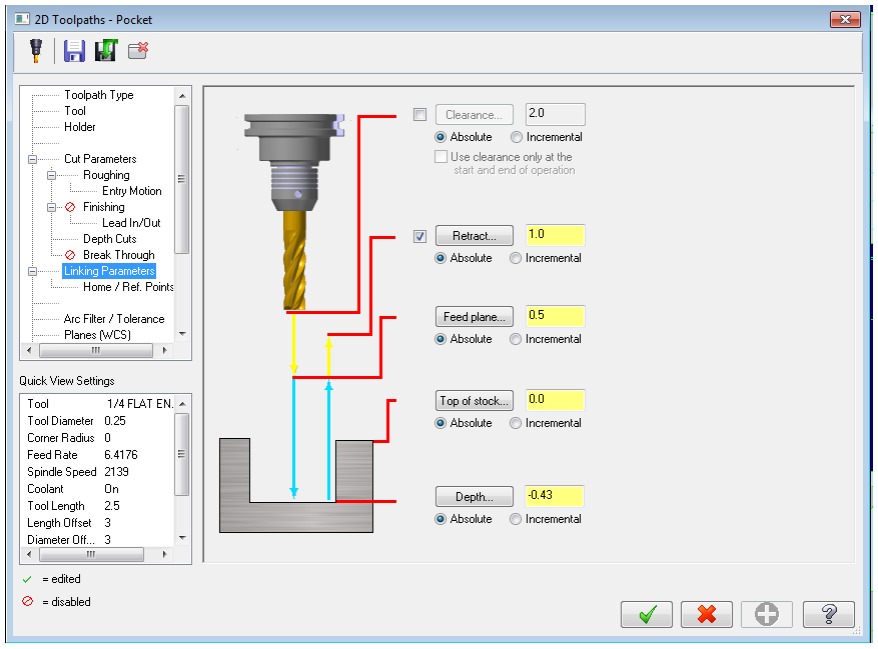
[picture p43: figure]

f. Select Depth Cuts from the options tree. This defines the depth of cut for each pass.
g. Max rough step is depth per pass. The computer figures out the number of passes necessary based on your maximum rough step. For aluminum with 0.5” cutter, 0.25” is a safe depth per pass.
h. Click the Green Checkmark

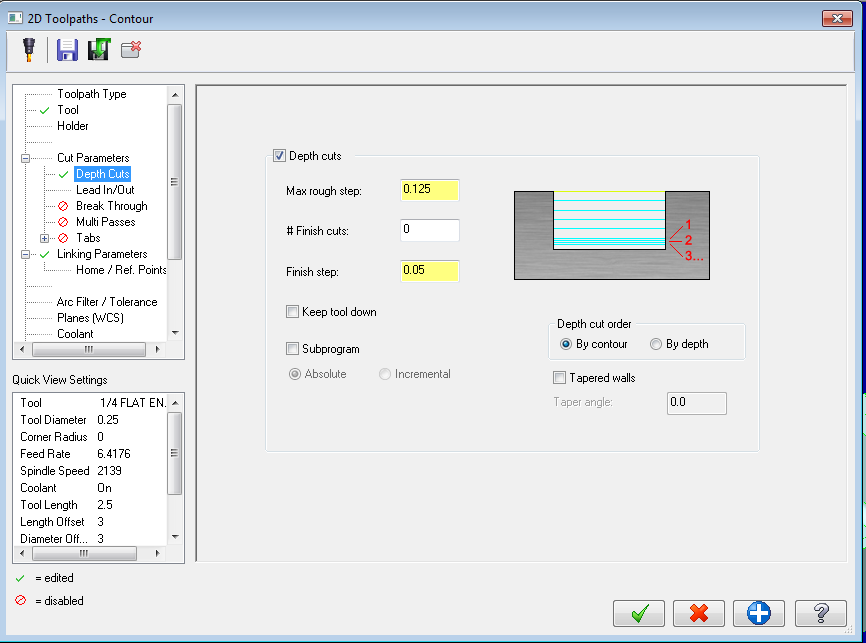
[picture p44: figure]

10. Click dropdown, Toolpaths > Pocket
a. For making a pocket with a bottom fillet, you must select the inner contour located on the floor of the pocket for the initial pocketing pass. Click the contours where you want the pocket to be.
b. Select the chain remembering to click just ahead of the red arrow each time until you get back to the green arrow
c. When finished, click the Green Checkmark
d. Select Cut Parameters from the options tree. Constant overlap and helix entry motion are common for pockets.
e. Set Depth Cuts and Linking Parameters the same as in the contour path.
f. Click the Green Checkmark
g. Click Geometry in the toolpath tree, then Right Click > Add Chain
i. If the toolpaths are on the wrong side, you can Right Click > Change Side, or Right Click > Reverse Chain.
11. Create fillet contour path
a. Click on the line at the top of the fillet against the wall. This is how you will leave the fillet when using a ball end or radiused end mill
12. Select all the programs on the left side (ctrl click) so they are all checkmarked, or simply click on the top Toolpath Group. Make sure all paths have a green checkmark next to them.

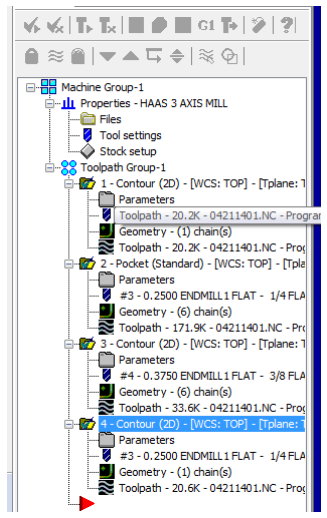
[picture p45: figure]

a. Click the G1 icon and then click the Green Checkmark
b. Save the output file to a thumb drive by dragging files from network location into a “Programs” folder on your thumb drive.
c. Put your thumb drive in the USB port on the side of the machine

## MACHINE OPERATION

13. Put the tools you want to use in the machine
a. Put each tool in the appropriate collet
b. Rotate the carousel until it is at the tool number you want to put the tool in (the same one you set as the Tool #, Len. Offset, etc.)
i. To rotate the carousel, push the MDI button for manual input, then push the ATC FWD or ATC REV to move to the next or previous tool.
ii. To skip to a specific tool, enter the tool code+number (ex: “T4”) in the input field, then push ATC FWD or ATC REV.
c. Push and hold the round, black button on the spindle column and align the two teeth on the spindle with the slots on the collet
d. Let go of the button when it is aligned, and the collet should be sucked up into the spindle.
14. Load the stock into the machine and square up the stock. For manual machining operation:
a. Click Hand Jog, then set your jog increment to .01”, then select an axial direction (ex: X-). You can either hold the axial direction button to jog, or you can use the hand wheel to jog. Note that each increment on the hand wheel is equal to the selected jog increment. This is how you will be able to manually direct the machine. You must be very careful to not crash the machine. When jogging the machine at a high rate, the machine coasts for a bit after you stop, so it is very easy, especially in the Z direction, to crash into things. Always check your selected axial direction and jog increment before jogging on the machine.
b. To start the spindle, push the MDI button and type your desired RPM into the input field (ex: “1500”) and then push the CW button.
c. To start the coolant, push the COOLNT button. If the coolant does not start, make sure the valve on the nozzles is open. You can control the flow rate using this valve.
d. Make sure to take off the vice handle before any machine operations.
e. You can push the JOG LOCK button and then push the axial direction you want to jog in. Push JOG LOCK again to stop the machine. Note that there are two ways to control the jog feed rate: the jog increment and the feed override. Make sure you have a reasonable jog feed rate before cutting by jogging away from your workpiece.
15. Define your Tool Offsets and Part Zeros for the stock. These should match the location of your coordinate system origin that you created in SolidWorks.
a. Define tool heights, which essentially defines the Z direction origin for each tool.

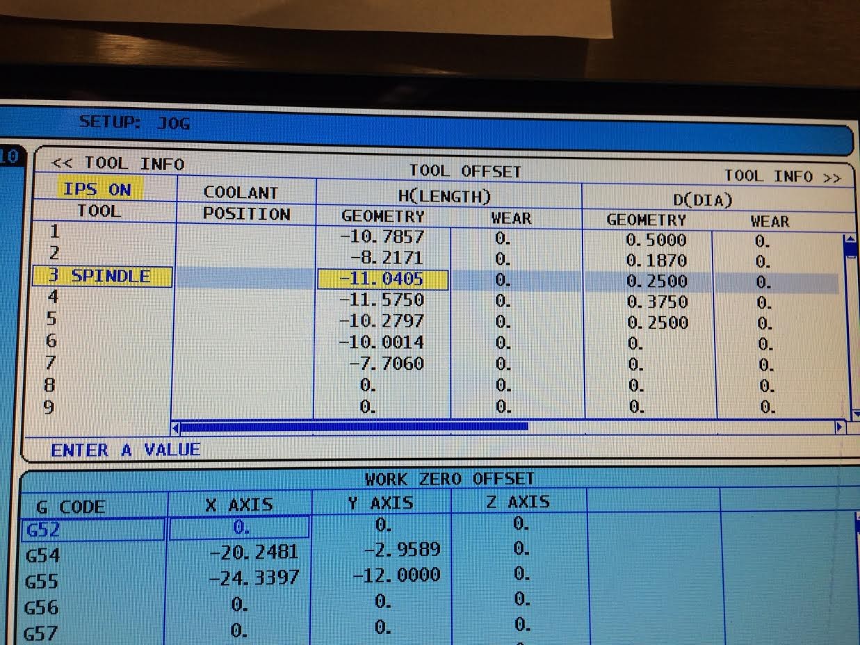
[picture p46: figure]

i. Jog each tool to down close to the surface of the part with the spindle off
ii. Take a piece of paper and put it between the tip of the cutter and the surface of the part
iii. Move the paper back and forth under the tool and move the head down very slowly (.001” jog increment) using the hand wheel until the paper is pinched between the tool and surface (the paper stops moving).
iv. Push the OFFSET button to get to the tool offset panel (the active panel background should be white)

v. Use the D-pad to move the cursor to highlight the appropriate H(LENGTH) GEOMETRY cell for the tool you are trying to zero (ex: Tool 3 in the photo above)
vi. Push TOOL OFFSET MEASURE. Because of the paper method used, you will still be between 0.001” to 0.003” above the part. This is generally within tolerance. For higher precision, use a different method.
vii. Switch tools and repeat for all tools in your program
b. Now we need to zero the work, which defines the X and Y direction origins.

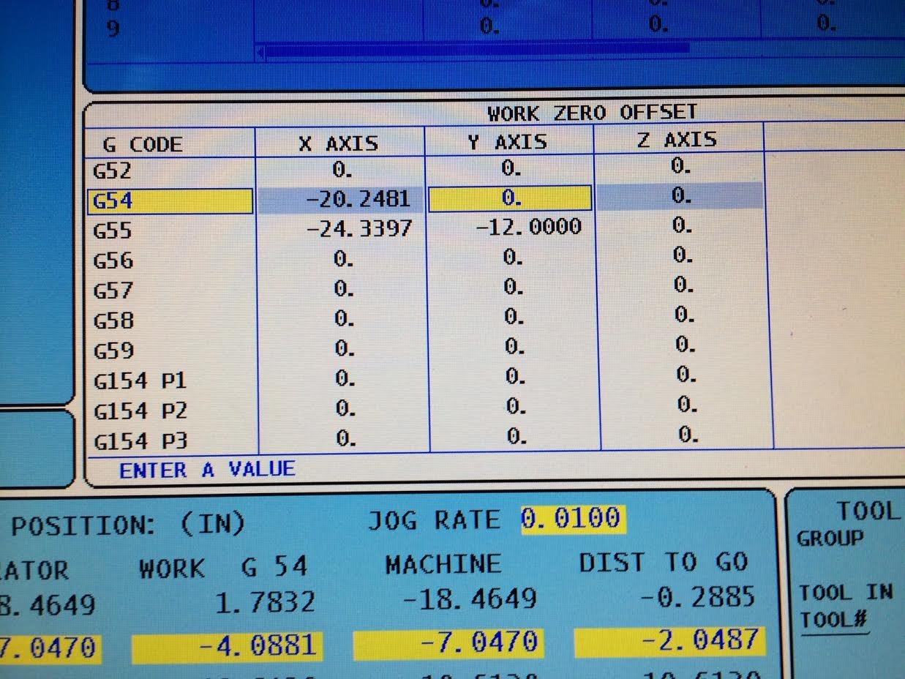
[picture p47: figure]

i. Jog the machine to the X and Y origin location using an edge finder tool or by some other method, depending on how you plan to machine your part.
ii. Push the OFFSET button to switch the active offset panel to WORK ZERO OFFSET
iii. | Make sure you are working in the G54 row
iv. | Move the cursor over to the X AXIS column and
push the PART ZERO SET button to zero X, then cursor over to the Y AXIS column to zero Y.
v. Do not change the Z AXIS part zero. This was set by your tool length offsets. You can set Z to a large positive number to make your program run above the part before cutting to check for errors. Be sure to make it larger than your deepest cut. To set this value, enter a value with decimal after the number (ex. “4.”) the hit F1, then hit Y on the keypad to confirm.
16. Import your program to the machine
a. Push LIST PROGRAM
b. Cursor over to the USB DEVICE tab, then push ENTER
c. Scroll to the program program file to highlight it d. Push SELECT PROGRAM, not ENTER
17. Preview the program graphically by pushing the SETNG GRAPH button twice, then push the green CYCLE START button. This will verify that there are no errors in the program. Keep an eye on the tool numbers to make sure the program is running as planned.
18. Run the program above your part as described in the part zero section above
a. Push MEM
b. Make sure to override your feed and rapid rate to very low speeds so you have time to observe and react in case the machine crashes. You can take the spindle to 0% if you want.
c. For this demo, we are using a 0.25” cutter at 1.5 plunge rate, 9.5 feed and 3000 RPM
d. Push CYCLE START and pay close attention to the toolpaths to make sure everything runs smoothly.
19. Run the final program
a. Push OFFSET to get the the work offset panel, scroll to the Z AXIS column in the G54 row, and enter “0.” in the input field, then push F1 to submit, Y to confirm. This resets your Z zero to the actual origin.
b. Push CYCLE START
c. Make sure the coolant comes on. If not, push the COOLNT button.
d. To pause the program, push FEED HOLD. To resume, push CYCLE START.
e. To stop spindle during feed hold, push STOP in the spindle override

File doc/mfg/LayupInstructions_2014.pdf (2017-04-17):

LV3 Airframe Module Layup Instructions

### Tips and Tricks

1. Staying clean and organized is very important.
2. A heat gun is super useful for dealing with the adhesive film. However, be careful not to let it get too hot. A little bit goes a long way.
3. Adhesive film is hard to remove from its backing, especially with gloves on. You can use the tongue depressor against the edge after sticking it to the part to get the backing off. Leave the blue side of the adhesive on.
4. The carbon sticks to the adhesive film too well, don’t stick it down unless you are sure it is in the correct spot.

### Procedure

1. Clean all surfaces and the floor using acetone, brooms etc.
2. Put on gloves
3. Arrange 4 work surfaces, each with a specific task:
a. Layup
b. Tool treatment
c. Cutting pieces of composite material
d. Aluminum mating ring treatment
4. Clean all the metal tools and part surfaces using acetone. Each part should cleaned thoroughly so that it leaves no visible residue on the towel.

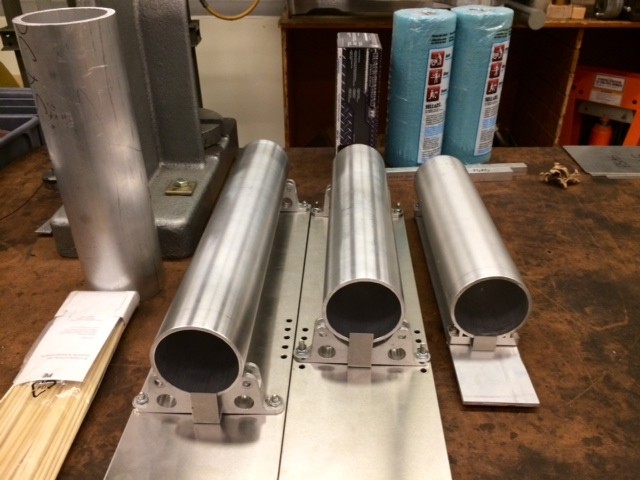
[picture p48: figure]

5. Wax the mandrels using Orca hybrid mold release according to the instructions on the can.
6. Similarly, wax the inside of the aluminum mating rings, making sure not to get any mold release on the carbon bond surfaces of the aluminum rings
7. Thoroughly sand the carbon bond surfaces of each aluminum mating ring to remove the oxide layer. When you’re finished sanding, the surfaces must be cleaned thoroughly with acetone.
8. Apply the 3M anti-galvanic corrosion agent to the bond surfaces by following the instructions on the package. In general, the solution should be applied with a brush constantly for about 3 minutes then left to dry and set for at least an hour.

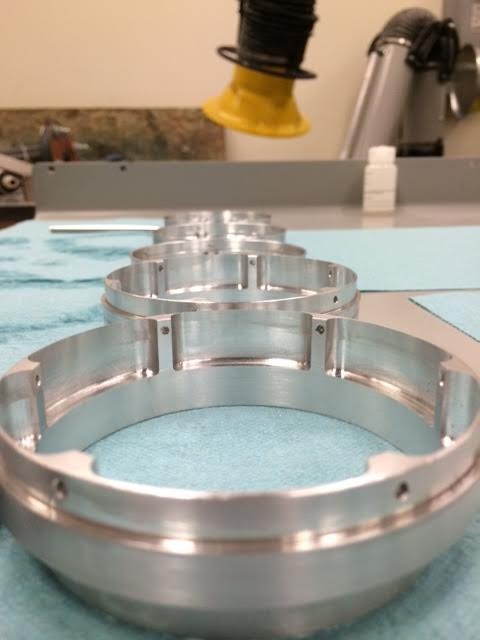
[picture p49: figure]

9. Cut the following layers using a sharp razor (except the core) and the cutout templates. Templates are labeled as steps 1-6.
Step 1: Cut 2 strips of aluminum step adhesive
Step 2: Cut 1 carbon inside ply
Step 3: Cut 1 inside film adhesive layer
Step 4: Mark with sharpie the outline of the honeycomb core layer. Use scissors to cut the core
Step 5: Cut 1 outside film adhesive layer
Step 6: Cut 1 carbon outside ply

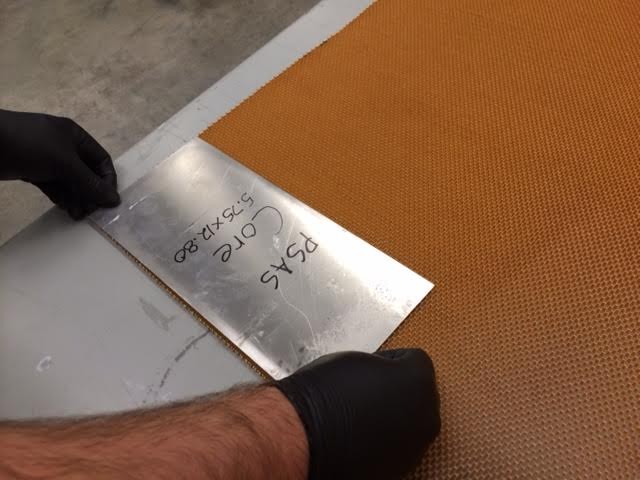
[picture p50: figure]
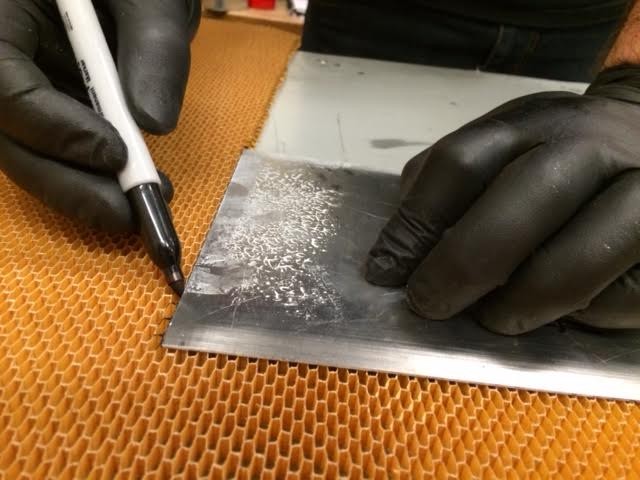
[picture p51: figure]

10. Lay everything out. If you need more than ~30minutes of time before laying up the module, the carbon and adhesive layers must be put back in the freezer until layup.

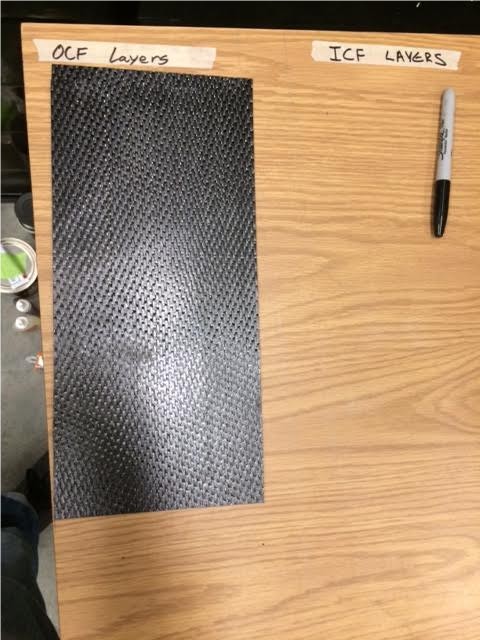
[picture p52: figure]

11. Slide the aluminum mating rings over the mandrel, making sure the orientation is correct
12. Slide the dummy layup rings onto the mandrel and fasten them to the mating rings
13. Fasten the dummy rings to the mandrel

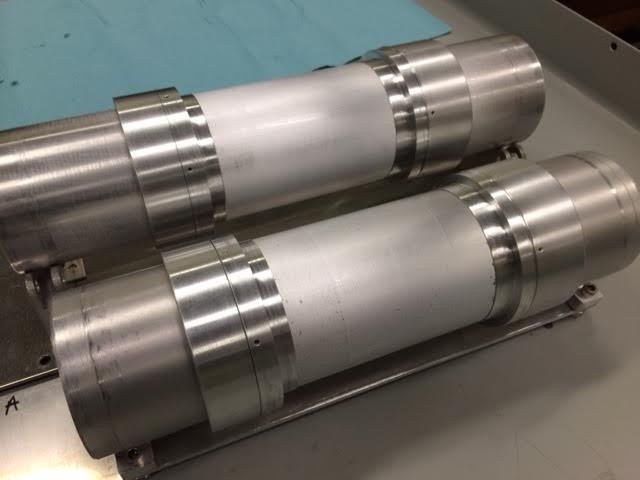
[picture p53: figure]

14. Wrap the two thin strips of adhesive around the lower bond surface of the mating rings.
15. Wrap the first layer of carbon. Make sure that the adhesive film layer underneath doesn’t move off of the step and onto the mandrel. It works best if one person does the aligning and the other rotates the mandrel. Wrap it snugly, but be sure to not introduce any warping of the fibers. Don't allow any air bubbles to remain.

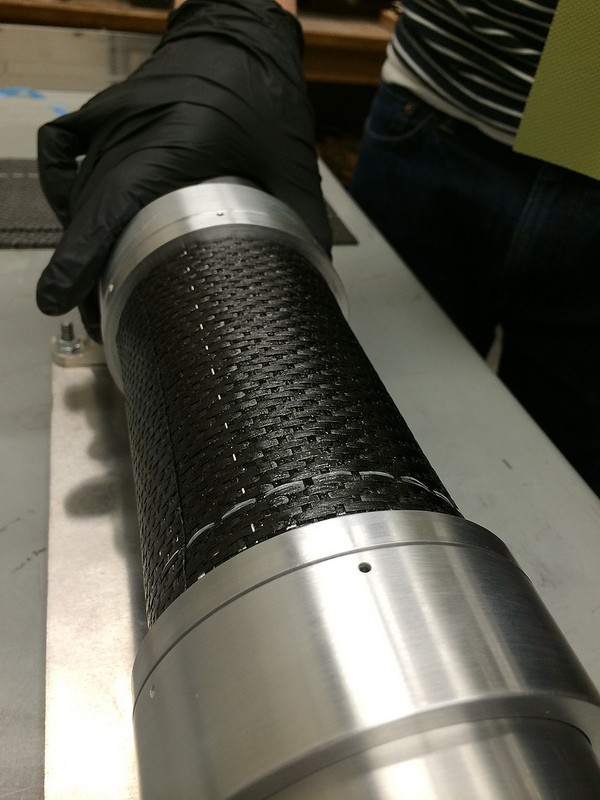
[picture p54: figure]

16. Use a tongue depressor in a rocking fashion (perpendicular to mandrel axis) to flatten out the carbon on top of the bond areas. This ensures good contact between the carbon and the bond area.

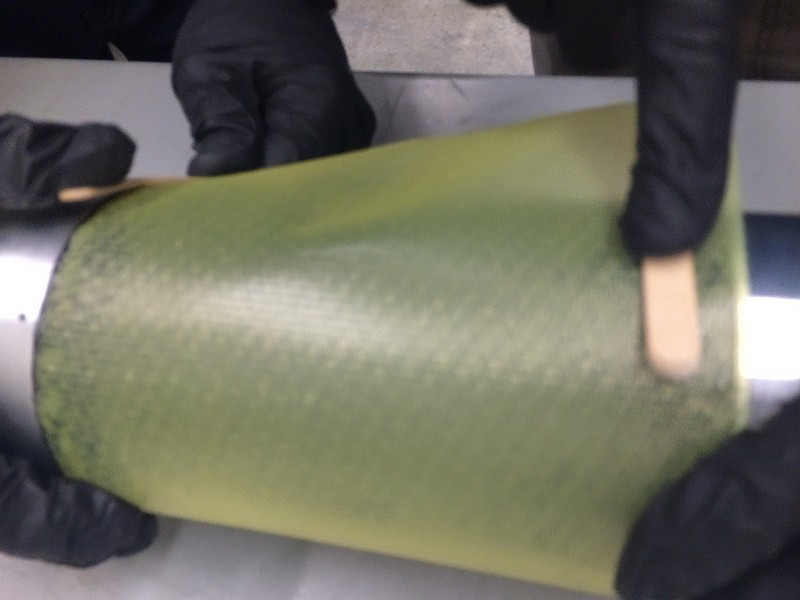
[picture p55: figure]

17. Wrap the inside layer of film adhesive on top of the carbon. Try to align the edges as well as possible, but it’s okay if there are wrinkles. The adhesive will melt and flow during cure.

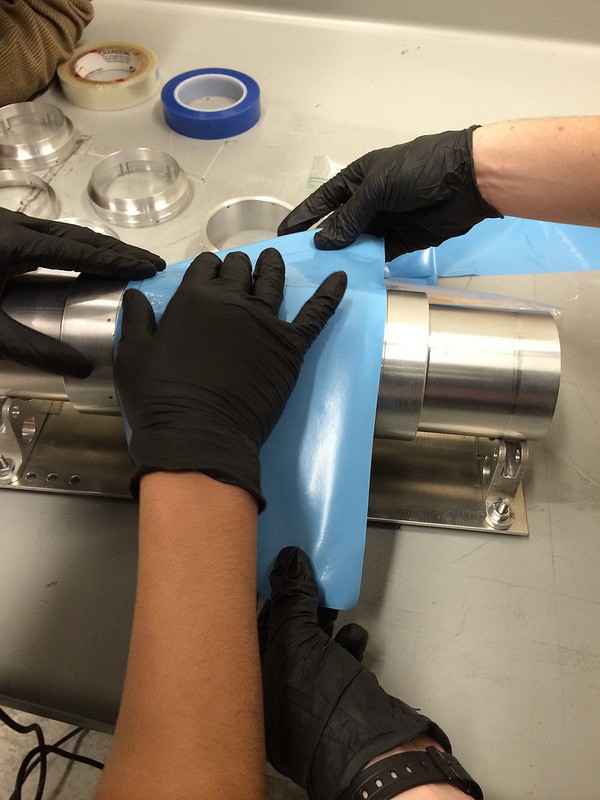
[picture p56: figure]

18. Wrap the honeycomb core layer. Use the heat gun sparingly to warm the adhesive underneath and press the core onto the adhesive to make it stick.
19. When you get to the end of the core wrap, compress the excess length of core and force it up against the other side. This compressed area will prevent gaps from forming at the core seam during cure.

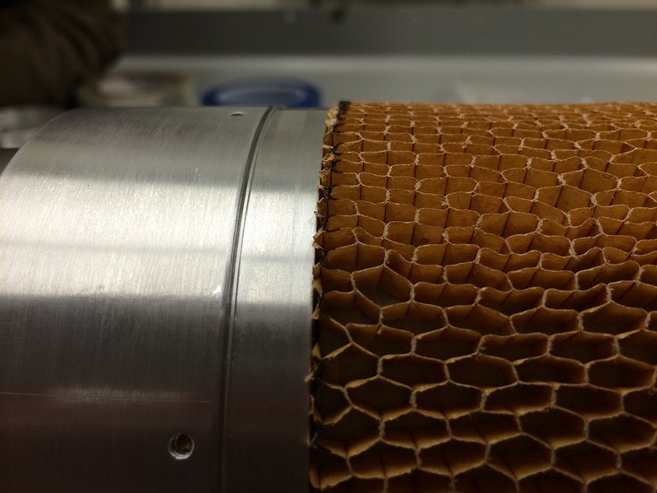
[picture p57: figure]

20. Wrap the outside layer of adhesive film. This one will go over both the core and rings. Try to align the edges of the adhesive with the step on the mating ring as well as possible.
21. Wrap the outside layer of carbon. Make sure that the lettering on the carbon does not end up on the outside of the module.

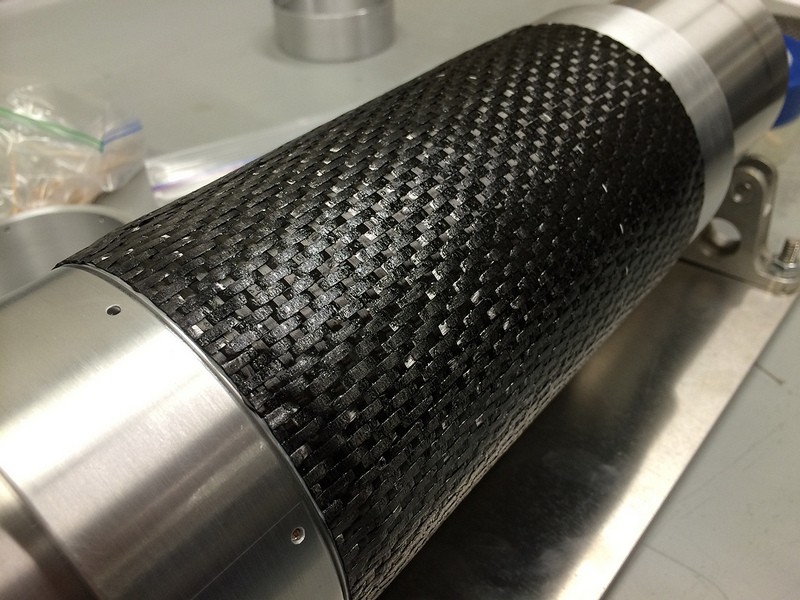
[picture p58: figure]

22. Wrap the perforated shrink tape across the length of the mandrel so that it overlaps itself 50% each time. Start the wrap on the dummy, taping it down well with the flash tape (clear blue). Then, have one person rotate the mandrel, one person hold the shrink tape roll, and one person align the tape as it is wrapped. The person aligning the shrink tape should also tension the tape so that it is taught as it is wrapped but not tight. End the shrink tape at the other dummy and secure it with flash tape.

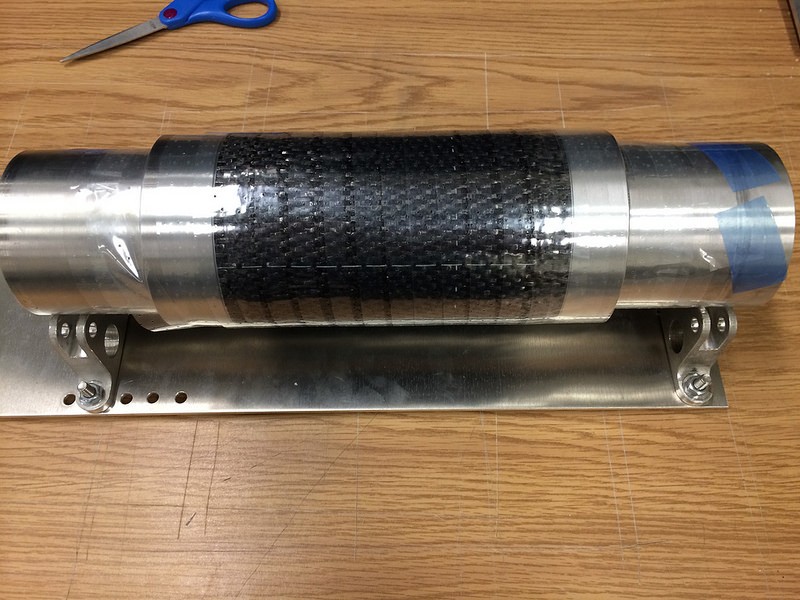
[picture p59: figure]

23. Wrap a diaper made from the breather cloth and use flash tape to secure it.

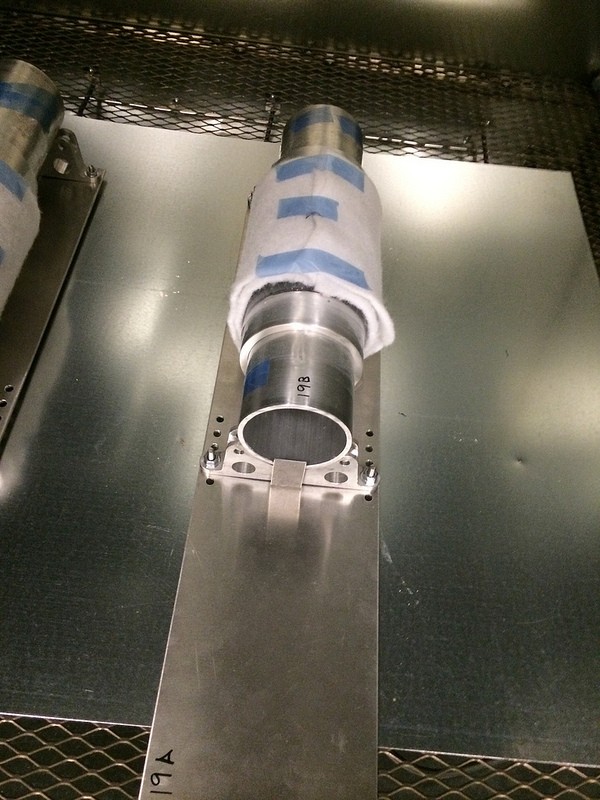
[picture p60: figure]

24. Put The mandrel into the oven on the aluminum stands
25. Turn on bake cycle. 3deg/min ramp up to 350F, where it is held for 2 hours.
26. Let cool slowly. The part will crackle as it cools down. This is normal.
27. Sometimes you have to hammer the parts off the mandrel. Whatever method you use, be sure not to damage the aluminum rings

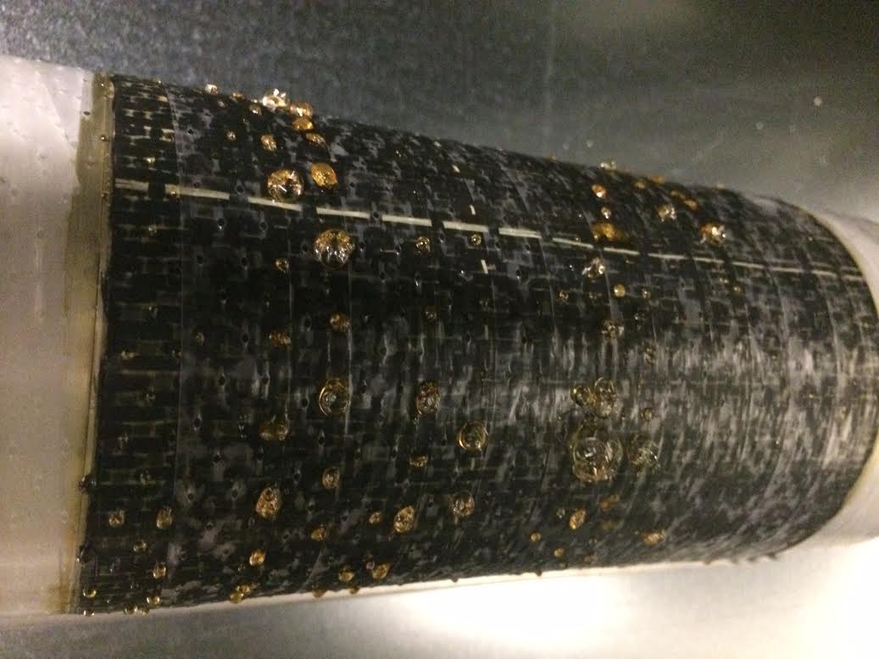
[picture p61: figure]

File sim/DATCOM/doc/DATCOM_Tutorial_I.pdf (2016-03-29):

# DATCOM Beginner’s Tutorial:

## Modeling a MiG-17

The method of building a model is DATCOM can be immensely confusing. There are no point-and-click interfaces here, only points in space. This tutorial aims at helping the novice user build a simple DATCOM model and test it. The numbers obtained may not be correct, but the model should be fairly accurate (except for a few assumptions).

### THE MIKOYAN-GUREVICH MIG-17

In 1949, the Mikoyan-Gurevich (MiG) design bureau began work on a new fighter to replace the MiG-15. Two features of the aircraft were a thinner wing of greater sweep and a redesigned tail that improved stability and handling at speeds approaching Mach 1 (speed of sound). Although similar in appearance to the MiG-15, the MiG-17 has more sharply swept wings, an afterburner, better speed and handling characteristics and is about three feet longer. The wings of the aircraft are midmounted, swept-back, and tapered with blunt tips. They have wide wing roots. The engine is one turbojet inside the body and has a round air intake in the nose. It has a single, small exhaust. The fuselage is short, thick, cigar-shaped and tapered to the rear. It has a blunt nose and bubble canopy. The tail fin is swept-back and tapered with rounded tip. Flats are high-mounted on the tail fin, swept-back, and tapered. Flats and fin overhang the exhaust. (GlobalSecurity.org) (http://www.globalsecurity.org/military/world/russia/mig-17.htm)

The MiG-17 was chosen for this tutorial because of its simple design. The fuselage cross-section is almost circular (and assumed to be), the wing shape is not complex, and the tails are not complex.

### DRAWINGS AND DIMENSIONS

The most difficult aspect of this project was finding adequate drawings of the aircraft which could provide accurate and consistent measurements. Eventually a drawing similar to the 3 view drawing pictured here was found. We can use the fact that MIG-17 has a wingspan of approximately 31 feet 7 inches and a length of 36 feet 5 inches to scale the drawing and get the dimensions needed.

It can be found (online) that the sweep of the wing and horizontal tail is 45 deg (approximately). The sweep of the large

vertical tail is taken to be 55 deg, although it may not be. The dihedral of the wing is -3

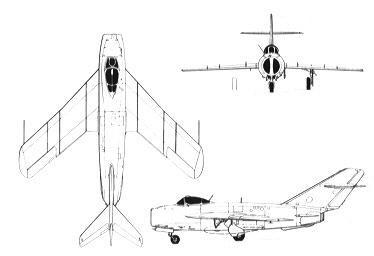
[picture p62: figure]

deg and the incidence is 1 deg.

As stated before, the fuselage cross section is conveniently circular, and for several stations, constant. It should be noted that the canopy was not implemented in the tutorial, which could possibly have affected the results (unimportant though).

A major hindrance of the project, however, is the airfoil. The MIG uses a TsAGI S-12 (12%) airfoil shape. Since planes don't fly without wings, and the airfoil shape has a profound impact on flight, the selection of the airfoil is critical. Furthermore, the Digital Datcom does not account for Russian

Figure 1: MiG 17 Views airfoils, so the assumption that a TsAGI S-12 (12%) is equivalent to a NACA 66-012 was made. Justification: none (aside from unverified information online). Since the data for TsAGI airfoils are not readily available, the characteristics cannot be inputted manually into DATCOM, therefore we are left having to make this assumption.

### WRITING THE for005.dat FILE

It would be wise to read section 3 (Definition of Inputs) of volume I of the Digital DATCOM manual, especially 3.1 and 3.2, to familiarize yourself for what is coming next.

The for005 file (aka input file) defines the flight characteristics and geometry of the aircraft. It follows a very specific format and any deviance for the format will cause the analysis not to be run.

First we input the CASEID on the first line:

CASEID MIKOYAN-GUREVICH MiG-17

Every piece of data that defines the flight characteristics and geometry of the aircraft is contained in namelists. In the input file, namelists are preceded by a "$" sign (ex. $FLTCON) and the statements are terminated with "$" signs. For this exercise we will use the following namelists:

FLTCON - defines the flight conditions
SYNTHS - locates the cg, wing, horizontal tail, and vertical tail with respect to a reference line
BODY - defines the body geometry
WGPLNF - defines the wing planform geometry
HTPLNF - defines the horizontal tail geometry VTPLNF - defines the vertical tail geometry

### THE FLTCON NAMELIST

The FLTCON namelist defines the flight conditions such as Mach number(s), altitude(s), and angle of attacks to be analyzed. A full list of the inputs can be found on page 27 of the Digital Datcom manual volume I. We will use the following variables from the FLTCON namelist:

NMACH - number of Mach numbers to be run. We will only run at one Mach.
MACH - the aformentioned Mach numbers to be run. We will run at Mach = 0.60.
NALPHA - the number of angles of attack to test. We will test at 10 AOA's.
ALSCHD - the schedule of angles of attack. We will use (in deg): -4, -2, 0, 2, 4, 6, 8, 10, 12, 14 (ten total)
NALT - number of altitudes to run. We will test only one altitude.
ALT - the altitudes to run. We will test at 5000 feet.
WT - the weight of the aircraft. We will use 13395 lbs for the MiG.
LOOP - we will set to 1. A discussion of the important LOOP parameter will be presented at some other time.

We can input these variables into the FLTCON namelist. Note that each number must contain a decimal point. Also, the file can only be a certain number of characters in horizontal length, so do not go over. The order in which the variables are given are not crucial, but the following format is recommended. The following describes what goes into the input file:

$FLTCON NMACH=1.0,MACH(1)=0.6,NALPHA=10.0,ALSCHD(1)=-4.0,-2.0, 0.0,2.0,4.0,6.0,8.0,10.0,12.0,14.0,NALT=1.0,ALT(1)=5000.0, WT=13395.0,LOOP=1.$

### THE SYNTHS NAMELIST

The SYNTHS (Synthesis) namelist is very important because it sets up the c.g. location as well as the position of the wing and tail surfaces. So at this point you should know the dimensions of the aircraft pretty well. Page 33 in Datcom Volume I indicates exactly what dimensions you will need.

All horizontal measurements will be taken from the nose of the aircraft. All vertical measurements will be taken from a reference line conveniently placed at the center of the aircraft. The following variables from the SYNTHS namelist will be used:

XCG - the horizontal position of the c.g. Since information of the c.g. position is not given, a c.g. position of 11.17 ft. was arbitrarily chosen (probably not right).
ZCG - the vertical position of the c.g. with respect to the reference line. Arbitrarily chosen as 0 feet.
XW - the horizontal position of the apex of the wing. Measured as 3.63 feet.
ZW - the vertical position of the wing apex wrt the reference line. Measured as 0.42 feet. ALIW - the incidence of the wing in degrees. For the MiG, this is 1 degree.
XH - the horizontal position of the apex of the horizontal tail. Measured as 28.73 feet.
ZH - the vertical position of the horiz. tail apex wrt the reference line. Measured as 5.24 feet. ALIH - incidence of the horizontal tail. No data found for the MiG, so taken as 0 degrees.
XV - the horizontal position of the apex of the vertical tail. Measured as 18.3 feet.
ZV - the vertical position of the vertical tail apex wrt the reference line. Since this lies on the reference line, it is 0 feet.
These numbers can be inputted into the SYNTHS namelist:

$SYNTHS XCG=11.17,ZCG=0.0,XW=3.63,ZW=0.42,ALIW=1.0,XH=28.73, ZH=5.24,ALIH=0.0,XV=18.3,ZV=0.0$

The following drawings will give the dimensions that will be used in this namelist and the subsequent ones.

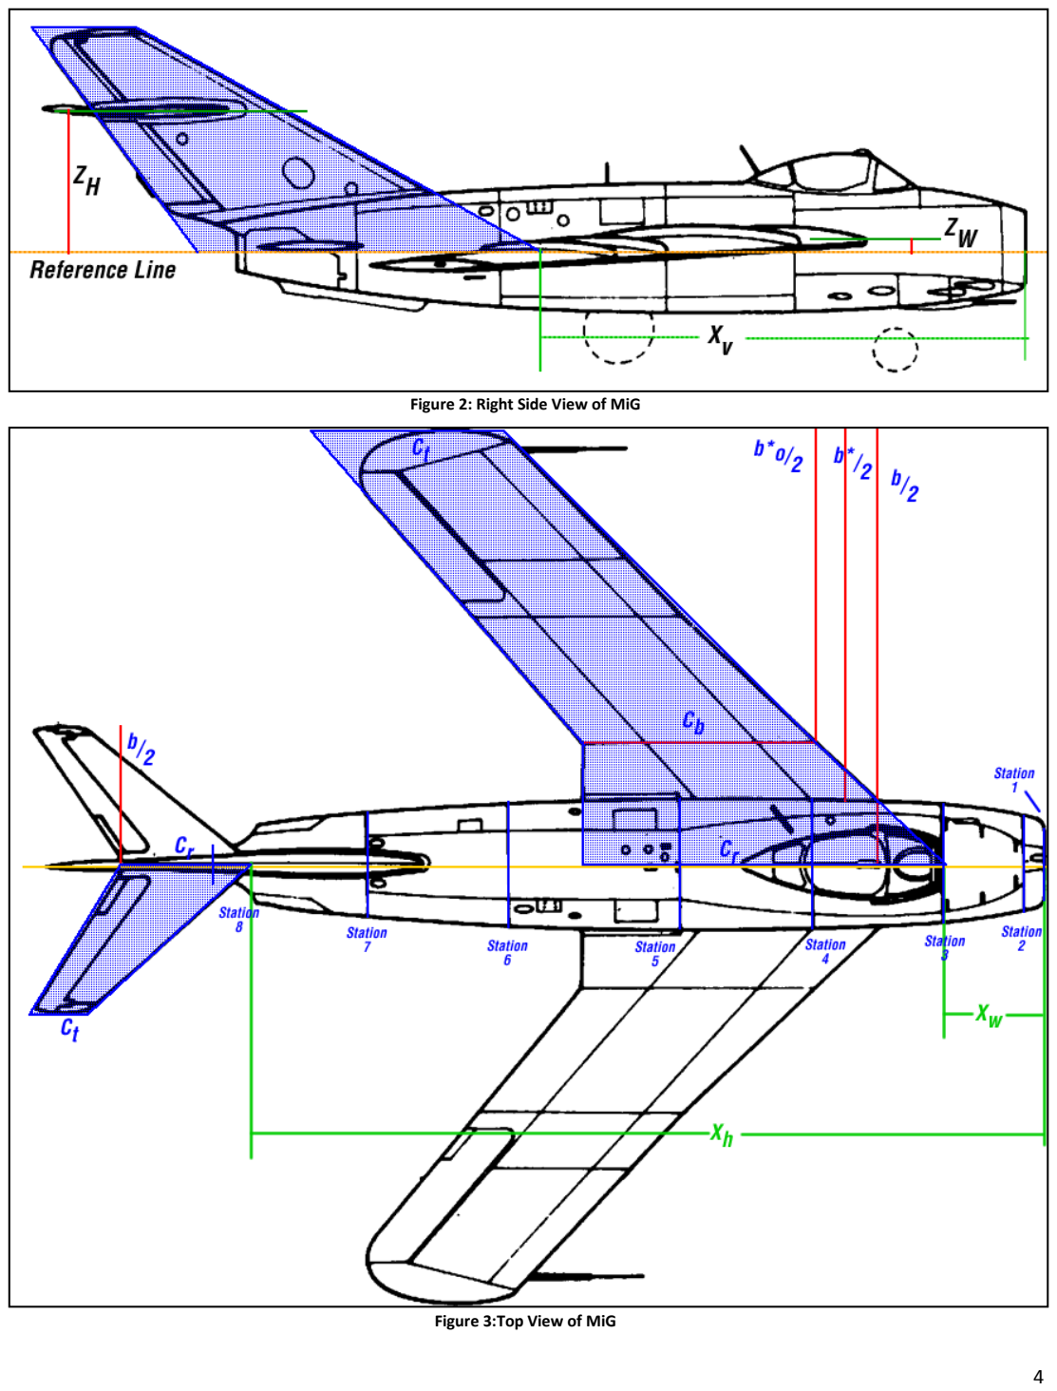
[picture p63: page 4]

Figure 2: Right Side View of MiG

Figure 3:Top View of MiG

### THE BODY NAMELIST

Now we can start modeling the components. First, we'll start with the body. As stated previously, we will forget the canopy and model the fuselage as having a circular cross section at each station. Note that in the drawing above, we have 8 stations starting with the nose and concluding at the rear section of the fuselage. We will need the horizontal distance from the nose at each station (Xdistance) as well as the cross sectional area at each station. The numbers are tabulated below:

Station | 1 | 2 | 3 | 4 | 5 | 6 | 7 | 8
X (feet) | 0.0 | 0.74 | 8.35 | 13.14 | 19.35 | 24.41 | 28.41 | 30.77
R (radius, feet) | 1.29 | 1.72 | 2.32 | 2.32 | 2.25 | 1.88 | 1.36 | 0.69
S (area, feet^2) | 5.19 | 9.32 | 16.89 | 16.89 | 15.94 | 11.12 | 5.85 | 2.5

The variables of the namelist BODY that we will use are:

NX - number of body stations
X - horizontal distance of each station
S - cross sectional area at each station
(Technically we could use "R" instead of "S", but there are problems with that later on)

With all of these values know, we can fully define the fuselage. The data is inputted as follows:

$BODY NX=8.0,
X(1)=0.0,0.74,8.35,13.14,19.35,24.41,28.41,30.77, S(1)=5.19,9.32,16.89,16.89,15.94,11.12,5.85,2.5$

### THE WGPLNF NAMELIST

Now we can define the wing planform using the WGPLNF namelist. Datcom volume I page 37 and 38 can be extremely helpful for all of the planforms. The drawings above fully prescribe the wing planform shape. The following are the variables we will use in defining the wing:

CHRDTP - the length of the chord at the tip of the wing. Measured to be 7.02 feet.
SSPNOP - the "Semi-Span outboard panel" which is "b*o/2" in the drawing. If the wing has two sections, like the MiG, there is an inboard panel and an outboard panel. This dimension is taken from the demarcation of the two panels to the tip chord. Measured to be 11.32 feet. SSPNE - the "exposed" semi-span, which is the "b*/2". This dimension is from the side of the fuselage to the tip chord. Measured to be 13.41 feet..
SSPN - the theoretical semi-span, which is b/2. This dimension is from the root chord to the tip chord. Measured to be 15.71 feet.
CHRDBP - the chord at the break point between the inboard and outboard panel (the "cb" in the drawing). Measured to be 8.4 feet.
CHRDR - the length of the chord at the root of the wing. Measured to be 14.0 feet.
SAVSI - the sweep of the wing at the inboard panel (refer to the manual). Although the sweep of the MiG differs from the inboard to the outboard panel, we will take this as constant and keep it as 45 degrees.
SAVSO - the sweep of the wing at the outboard panel. A stated before, it will be 45 deg.

TWISTA - the twist angle of the wing (wash-out). For the MiG, it is 0 deg.
CHSTAT - the % of the mac at which the sweep angle will be referenced. Usually this is c/4 or 0.25.
DHDAHI - the dihedral of the inboard panel. If the inboard and outboard panel dihedral is the same (constant dihedral across the wing), then only DHDADI is inputted. For the MiG, the wing dihedral is -3 deg.
TYPE - different planform types (refer to manual). Will be set to 1.

These values are inputted into the for005 file as follows:

$WGPLNF CHRDTP=7.02,SSPNOP=11.32,SSPNE=13.41,SSPN=15.71, CHRDBP=8.4,CHRDR=14.0,SAVSI=45.0,SAVSO=45.0,CHSTAT=0.25, TWISTA=0.0,DHDADI=-3.0,TYPE=1.0$

### THE HTPLNF NAMELIST

The horizontal tail is described the same way as wing using the same variables. Because the geometry of the HT is simpler, we will only use the following variables: CHRDTP, SSPNE, SSPN, CHRDR, SAVSI, CHSTAT, and TYPE.

CHRDTP is 1.86 feet
SSPNE is 5.42 feet
SSPN is 5.43 feet
CHRDR is 4.69 feet
SAVSI is 45 degrees
CHSTAT is 0.25
TYPE is 1

And so the values are inputted into the HTPLNF namelist as follows:

$HTPLNF CHRDTP=1.86,SSPNE=5.42,SSPN=5.43,CHRDR=4.69,SAVSI=45.0, CHSTAT=0.25,TYPE=1.0$

### THE VTPLNF NAMELIST

The vertical tail is described the same way as wing using the same variables. Because the geometry of the VT is simpler, we will only use the following variables: CHRDTP, SSPNE, SSPN, CHRDR, SAVSI, CHSTAT, and TYPE.

CHRDTP is 3.76 feet
SSPNE is 6.05 feet
SSPN is 8.18 feet
CHRDR is 12.47 feet
SAVSI is 55 degrees (not measured) CHSTAT is 0.25

TYPE is 1

And so the values are inputted into the VTPLNF namelist as follows:

$VTPLNF CHRDTP=3.76,SSPNE=6.05,SSPN=8.18,CHRDR=12.47,SAVSI=55.0, CHSTAT=0.25,TYPE=1.0$

### AIRFOIL DESIGNATIONS

We cannot forget to input the airfoil shapes for the wing and tails. Page 74 and 75 of volume I has some information on this. If the wing was a NACA-2412, we would input into the for005 file: NACA-W-4-2412. The "NACA" indicates that it is a NACA airfoil, for which DATCOM has built in data. "W" indicates that the airfoil is to be applied to the wing ("H" for HT, and "V" for VT). "4" indicates that it is a 4 series airfoil (DATCOM accepts 1, 4, 5, and 6 series airfoils). And after that is the airfoil designation number, in this example it is "2412."

For the MiG, the NACA 66-012 airfoil we be used for the wing, and the 66-009 for the tails. They will simply be inputted into DATCOM as follows:

NACA-W-6-66-012
NACA-H-6-66-009
NACA-V-6-66-009

### TERMINATING THE FILE

There are a number of commands that can be placed at the end of the file to specify information and give more data. We will use 3 commands:

DIM FT - specifies that all of the dimension were given in feet and all out the output should be in "English" units
BUILD - show the data for all of the components. not just the aircraft
PLOT - generate a plot file (for013.dat) to input into the MATLAB plotting program

Finally, the file ends with "NEXT CASE". In the input file this looks like:

DIM FT
BUILD
PLOT
NEXT CASE

### THE FULL for005.dat FILE

Here is the full input file that will be run by DATCOM.

CASEID ----- MIKOYAN-GUREVICH MiG-17 -----
$FLTCON NMACH=1.0,MACH(1)=0.6,NALPHA=10.0,ALSCHD(1)=-4.0,-2.0, 0.0,2.0,4.0,6.0,8.0,10.0,12.0,14.0,NALT=1.0,ALT(1)=5000.0, WT=13395.0,LOOP=1.$
$SYNTHS XCG=11.17,ZCG=0.0,XW=3.63,ZW=0.42,ALIW=1.0,XH=28.73, ZH=5.24,ALIH=0.0,XV=18.3,ZV=0.0$
$OPTINS SREF=243.0$
$BODY NX=8.0,
X(1)=0.0,0.74,8.35,13.14,19.35,24.41,28.41,30.77, S(1)=5.19,9.32,16.89,16.89,15.94,11.12,5.85,2.5$ NACA-W-6-66-012
$WGPLNF CHRDTP=7.02,SSPNOP=11.32,SSPNE=13.41,SSPN=15.71, CHRDBP=8.4,CHRDR=14.0,SAVSI=45.0,SAVSO=45.0,CHSTAT=0.25, TWISTA=0.0,DHDADI=-3.0,DHDADO=-3.0,TYPE=1.0$
NACA-H-6-66-009
$HTPLNF CHRDTP=1.86,SSPNE=5.42,SSPN=5.43,CHRDR=4.69,SAVSI=45.0, CHSTAT=0.25,TYPE=1.0$
NACA-V-6-66-009
$VTPLNF CHRDTP=3.76,SSPNE=6.05,SSPN=8.18,CHRDR=12.47,SAVSI=55.0, CHSTAT=0.25,TYPE=1.0$
DIM FT
BUILD
PLOT
NEXT CASE

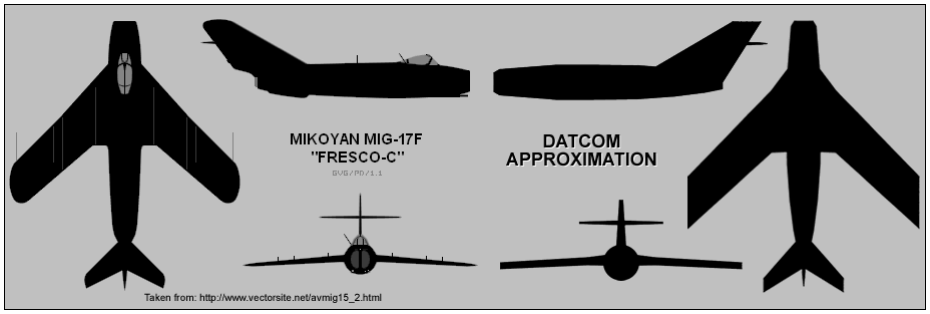
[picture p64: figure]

REFERENCES

Data and History

Blueprints of Mig-17, http://www.the-blueprints.com
History, http://www.globalsecurity.org/military/world/russia/mig-17.htm
History & Data, http://www.vectorsite.net/avmig15_2.html
Pictures, http://www.suchoj.com/galerie/index.htm?http://www.suchoj.com/andere/MiG-17/galerie.shtml (http://www.suchoj.com/galerie/index.htm?http://www.suchoj.com/andere/MiG-17/galerie.shtml)

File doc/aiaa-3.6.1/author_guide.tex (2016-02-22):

%
% `author_guide.tex' - AIAA author instructions that use the AIAA class.
%
% Typical processing for PostScript (PS) output:
%
%  latex author_guide
%  bibtex author_guide  (bibliography)
%  makeindex -s nomencl.ist -o author_guide.gls author_guide.glo (nomenclature)
%  latex author_guide   (repeat as needed to resolve references)
%
%  xdvi author_guide    (onscreen draft display)
%  dvips author_guide   (postscript)
%  gv author_guide.ps   (onscreen display)
%  lpr author_guide.ps  (hardcopy)
%
% With the above, only Encapsulated PostScript (EPS) images can be used.
%
% Typical processing for Portable Document Format (PDF) output:
%
%  pdflatex author_guide
%  bibtex author_guide  (bibliography)
%  makeindex -s nomencl.ist -o author_guide.gls author_guide.glo (nomenclature)
%  pdflatex author_guide      (repeat as needed to resolve references)
%
%  acroread author_guide.pdf  (onscreen display)
%
% If you have EPS figures, you will need to use the epstopdf script
% to convert them to PDF because PDF is a limmited subset of EPS.
% pdflatex accepts a variety of other image formats such as JPG, TIF,
% PNG, and so forth -- check the documentation for your version.
%
% If you do *not* specify suffixes when using the graphicx package's
% \includegraphics command, latex and pdflatex will automatically select
% the appropriate figure format from those available.  This allows you
% to produce PS and PDF output from the same LaTeX source file.
%
% To generate a large format (e.g., 11"x17") PostScript copy for editing
% purposes, use
%
%  dvips -x 1467 -O -0.65in,0.85in -t tabloid author_guide
%
% For further details and support, read the Users Manual, aiaa.pdf.
%
% This software is released under the terms of the LaTeX Project Public
% License.  Copyright (C) 2004 by Bil Kleb, Bill Wood, and Erich Knausenberger.

\documentclass{aiaa-tc}% insert '[draft]' option to show overfull boxes

 \usepackage{wrapfig}% embedding figures/tables in text (i.e., Galileo style)
 \usepackage{threeparttable}% tables with footnotes
 \usepackage{dcolumn}% decimal-aligned tabular math columns
  \newcolumntype{d}{D{.}{.}{-1}}
 \usepackage{nomencl}% automatic nomenclature generation via makeindex
  \makeglossary
 \usepackage{subfigure}% subcaptions for subfigures
 \usepackage{subfigmat}% matrices of similar subfigures, aka small mulitples
 \usepackage{fancyvrb}% extended verbatim environments
  \fvset{fontsize=\footnotesize,xleftmargin=2em}
 \usepackage{lettrine}% dropped capital at beginning of paragraph
 \usepackage[dvips]{dropping}% alternative dropped capital package
 \usepackage{hyperref}% embedding hyperlinks [must be loaded after dropping]

 \title{Preparation of Papers for\\
        AIAA Technical Conferences}

 \author{%
  First A. Author\thanks{Job Title, Department, Address, and AIAA
                              Member Grade.}
  \ and
  Second B. Author\thanksibid{1}\\% same footnote as 1st author\\
  {\normalsize\itshape
   Business or Academic Affiliation, City, Province, Zipcode, Country}\\
  \and
  Third C. Author\thanks{Job Title, Department, Address, and AIAA
                              Member Grade.}\\
  {\normalsize\itshape
   Another Business or Academic Affiliation, City, Province, Zipcode, Country}
 }

 \AIAApapernumber{200?-????}
 \AIAAconference{Conference Name, Date, and Location}
 \AIAAcopyright{\AIAAcopyrightD{200?}}

 % define some commands to maintain consistency
 \newcommand{\pkg}[1]{\texttt{#1}}
 \newcommand{\cls}[1]{\textsf{#1}}
 \newcommand{\file}[1]{\texttt{#1}}

\begin{document}

\maketitle

\begin{abstract}
These instructions give you guidelines for preparing papers for AIAA
Technical Conferences.
Use this document as a guide if you are using \LaTeXe.
Otherwise, use this document as an instruction set.
Should this submission be for a non-electronic meeting, the electronic
file of your paper will be formatted further at AIAA.
Define all symbols used in the abstract.
Do not cite references in the abstract.
The footnote on the first page should list the Job Title and AIAA Member
Grade for each author.
\end{abstract}

\printglossary% creates nomenclature section produced by MakeIndex

\section{Introduction}

\lettrine[nindent=0pt]{T}{his} document is a \LaTeX\ template.
If you are reading a hardcopy or PDF version of this document, please
download the \LaTeX\ macros and sample files from
\href{http://www.ctan.org/}{www.ctan.org}
so you can use it to prepare your manuscript.
The \cls{aiaa-tc} class uses Computer Modern (CM) fonts, which
are part of any standard \TeX installation.
Use the \LaTeX\ files for formatting purposes,
but please see \file{author\_guide.pdf} for specific layout instructions.
Authors will first need to save the \cls{AIAA} files to their
working directory or install them into their \TeX\ distribution.

\section{Procedure for Paper Submission}

All manuscripts are to be submitted electronically via the AIAA
submission tool at \href{http://www.aiaa.org/author}{www.aiaa.org/author}.
Select the ``Submit a Paper to an AIAA Conference'' link, then click the
``Edit Old'' button.
When you submitted your abstract for review, you should have received a
tracking number for your paper.
Use this tracking number, along with the last name of the corresponding
author, to gain access to the AIAA Author Status Page.
This site will allow you to track your paper's status, update submission
data, select a copyright statement, and upload your manuscript.

Before you can upload your manuscript, you will need to select a
copyright statement to appear on your paper.
This can be achieved by clicking the ``Copyright Information'' link on
the Author Status Page.
Be sure to read the instructions and specific statements carefully
before selecting a statement for your manuscript.

Once you have selected a copyright statement, you can use the ``Upload
Manuscript'' feature of the Author Status Page to upload your paper.
All accepted authors will be notified by AIAA of the relevant
submission deadlines.
In addition, the deadlines for every conference can be found under the
conference title on the Author Status Page.

As with the submission of your abstract, be sure the name of the file
you upload for processing is short and simple (i.e., ``msc12345.tex'')
with no spaces, tildes, symbols, or other unusual characters.
If the file being uploaded is in \LaTeX, the document must be based
on \cls{article.cls} (this AIAA class is based on this class).
Failure to meet these requirements could result in a processing error
that would require you to re-upload your manuscript.%
\footnote{If you are uploading a PDF or postscript file, please do not
  include foreign (i.e., non-Roman alphabet) fonts.}
If you encounter difficulties with the upload and/or conversion of your
manuscript, please contact AIAA Papers Tech Support for assistance at
\href{mailto:paper_tech_support@aiaa.org?subject=upload}%
     {paper\_tech\_support@aiaa.org}.

\section{General Guidelines}

The following section outlines general (non-formatting) guidelines to
follow, drawn from the original AIAA Manuscript Preparation Kit.
These guidelines are applicable to all authors (except as noted), and
include information on the policies and practices relevant to the
publication of your manuscript.

\subsection{Publication by AIAA}

Your manuscript cannot be published by AIAA if:
\begin{enumerate}
 \item It has been published previously or
 \item An appropriate copyright statement has not yet been selected.
\end{enumerate}

\subsection{Paper Review and Visa Considerations}

It is the responsibility of the author to obtain any required government or
company reviews for their papers in advance of publication.
Start early to determine if the reviews are required; this process can
take several weeks.

If you plan to attend an AIAA technical conference or professional
development course held in the United States and you require a visa for
travel, it is incumbent upon you to apply for a visa with the
U.S. embassy (consular division) or consulate with ample time for
processing.
To avoid bureaucratic problems, AIAA strongly suggests that you submit
your formal application to U.S. authorities a minimum of 120 days in
advance of the date of anticipated travel.

Prospective conference and course attendees requiring a visa to travel
to the United States should first contact AIAA to request an official
letter of invitation.
This letter and a copy of the conference call for papers should be presented
along with the required documentation to the U.S. consular officials as part of
the formal application process.
AIAA cannot directly intervene with the U.S. Department of State,
consular offices, or embassies on behalf of individuals applying for visas.
A letter of invitation can be requested at
\href{http://www.aiaa.org/visa-info/}{www.aiaa.org/visa-info/} or you
may contact AIAA Customer Service at
\href{mailto:custserv@aiaa.org?subject=visa}{custserv@aiaa.org} for more
information.

\subsection{Tracking Number vs Paper Number}

Your paper was assigned a tracking number at the time you submitted
your abstract.
That number plus the corresponding author's last name is used to access
the AIAA Author Status Page.
This number is also useful when contacting AIAA technical support
regarding submission difficulties.
The tracking number is not the final AIAA paper number.
Once the abstract is accepted and assigned to the program, an AIAA
paper number is created.
The paper number, which appears in the format
{\footnotesize\textsf{AIAA-YEAR-NNNN}}, will be used to refer to your
paper in the program and in any publication format.
Do not include a paper number anywhere on your paper, as this number
will be stamped automatically in the top right corner of your paper at
the time of processing.

\subsection{Copyright}

Before AIAA can print or publish any paper, the copyright information
must be completed on the AIAA Web site.
Failure to complete the form correctly could result in your paper not
being published.
The following fields must be completed:
\begin{enumerate}
 \item Clearance Statement
 \item Non-Infringement Statement
 \item Publication Status Statement
 \item Copyright Assignment Statement
\end{enumerate}
For the Copyright Assignment Statement, select either A, B, C, or~D.
Be sure to read the copyright statements carefully.
If you are not sure which copyright statement to use, contact your legal
department; AIAA cannot help you determine which statement to use.
A hardcopy of the form is found in the Author Kit for your reference.
As you will be completing this form online, you do not need to fill out
the hard-copy form. Please do not upload the copyright form with your
paper, and do not include a copyright statement anywhere on your
paper. The correct statement will be stamped automatically at the time
of processing.

\subsection{Submission Deadlines}

\subsubsection{Meetings with Electronic Proceedings}

Manuscripts will be accepted for upload to the system from the receipt
of the acceptance letter to the beginning of the conference. You will be
notified of the specific manuscript submission deadline in your
acceptance letter, and the deadline will also be listed on the Author
Status Page for your paper. We ask that authors not upload a draft version
of their manuscript with the intent to upload a final version  later.
\emph{PLEASE upload only the final version of your manuscript.}

On-line conference proceedings will be made accessible to attendees
who have registered for the "full conference" option two weeks prior to
the conference. Please keep that date in mind when preparing and
uploading the final manuscript.

To ensure conference quality, session chairs will enforce a "no paper,
no podium" rule. This policy states that if your manuscript is not
uploaded to the Web site prior to your presentation, you will not be
allowed to present the paper at the conference. There are times when the
organizers at the conference request an earlier deadline than the beginning
of the conference. If such a situation arises, you will be notified in your
Author Acceptance Letter.

\subsubsection{Loose Papers Meetings}

The manuscript submission deadline for loose papers meetings is generally
six to eight weeks in advance of the event; you will be notified of the specific
deadline in your acceptance letter, and the date will also appear on the
Author Status Page for your paper. Papers uploaded before the deadline
will be reproduced and shipped to the conference by AIAA at no charge.

Authors who miss the electronic submission deadline will be expected to
hand-carry 100 copies of their paper to the meeting, and must still upload
their final manuscript to the AIAA Web site before the start of the conference
for their paper to be published. A general No paper, no podium rule is in
effect for all AIAA conferences. If your paper is not submitted to AIAA prior to
your presentation, you will not be allowed to present. If you miss the initial
deadline, contact your session chair or the conference Technical Chair for
further instructions.

\subsection{Color Illustrations}

Papers published electronically (online or on CD-ROMs) will be
reproduced in color automatically. If your paper is submitted to a loose
papers meeting (as specified in the author acceptance letter), color
printing can be arranged for an additional charge. Please contact the
technical papers specialist for details at 
\href{mailto:bettyg@aiaa.org?subject=illustrations}%
        {bettyg@aiaa.org}.

\section{Detailed Formatting Instructions}

\subsection{Document Text}

The default font for AIAA papers written in \LaTeX\ is 10-point Computer
Modern (CM).

\subsection{Title, Authors' Names, and Affiliations}

The title of your paper should be coded as \verb|\title{Paper Title}|,
with capital and lower-case letters, and centered at the top of the
page.
The names of the authors, business or academic affiliation, city, and
state/province should follow on separate lines below the title.
The names of authors with the same affiliation can be listed on the same
line above their collective affiliation information.
The authors' names, contact information, and affiliation is coded within
\LaTeX's standard \verb|\author| using \verb|tabular| environment
conventions and the \verb|\thanks| and \verb|\and| commands.
The affiliation line for each author includes the author's city, state,
and zip/postal code (or city, province, zip/postal code and country, as
appropriate).
The contact information for each author is given by the \verb|\thanks|
command and should include job title, department name, street
address/mail stop, and the AIAA member grade.
If this information is the same for two or more authors, the subsequent
authors should use the \verb|\thanksibid{}| command which requires the
number of the duplicate author contact information.
Author names are centered, and affiliations are centered and in italic type.
The title is created by the \verb|\maketitle| command.
For example,
\begin{Verbatim}
 \documentclass{aiaa-tc}
  \title{Paper Title}
  \author{%
    Bil Kleb\thanks{Aerospace Engineer, Aerothermodynamics Branch,
                    Mail Stop 408a, Lifetime AIAA member.}
    and Bill Wood\thanksibid{1}\\
    {\itseries NASA Langley Research Center, Hampton, Virginia, 23681}
    \and% issues a \end{tabular} followed by a \begin{tabular}{c}
    Someone Else\thanks{Job title, department name, street
                        address/mailstop, AIAA member grade.}\\
    {\itseries Business or Academic Affiliation, City, State, Zipcode}
  }
 \begin{document}
 \maketitle
\end{Verbatim}

\subsection{Headings}

AIAA Technical Conferences style defines 3 levels of section
headings:
\begin{description}
 \item Level 1 heading (\verb"\section"): bold, larger font, centered,
       and numbered with Roman numerals.
 \item Level 2 heading (\verb"\subsection"): bold, flush left, and
       numbered with capital letters.  No opening paragraph indentation.
 \item Level 3 heading (\verb"\subsubsection"): italic, flush left, and
       numbered with Arabic numbers (e.g., 1, 2, 3).  No opening
       paragraph indentation.
\end{description}

\subsection{Abstract}

The abstract should appear at the beginning of your paper.
It should be one paragraph long (not an introduction) and complete in
itself (no reference numbers).
It should indicate subjects dealt with in the paper and state the
objectives of the investigation.
Newly observed facts and conclusions of the experiment or argument
discussed in the paper must be stated in summary form; readers should
not have to read the paper to understand the abstract.

\subsection{Footnotes and References}

Footnotes, where they appear, should be placed above the 1-inch margin at
the bottom of the page.
To insert footnotes, use \verb|\footnote{}| as normal.
Footnotes are formatted automatically in \verb|aiaa.cls|, but if
another medium is used, they should appear in as superscript lower case
letters.
When adding notes to tables, e.g., as accommodated by the
\pkg{threeparttable} package, the symbols are down by hand and should be
in the sequence, *, $\dagger$, $\ddagger$, $\mathsection$,
$\mathparagraph$, $\|$, **, $\dagger\dagger$, and so forth.
This sequence should beginning anew with each table.

List and number all bibliographical references at the end of the paper.
Corresponding superscript numbers are used to cite references in the
text using the \verb|\cite{}| command,\cite{sutton:85ar} unless the
citation is an integral part of the sentence (e.g., ``It is shown in
Ref.~\citen{miner:75ncr} that\ldots[.]'') 
or follows a mathematical expression: ``$A2 + B = C$
(Ref.~\citen{wirin:90cp}).''
For this case, the command, \verb|\citen{}| is used.
\cite{*}% to load all refences for demonstration purposes which follow
Multiple citations are sorted and punctuated automatically through the
\cls{aiaa-tc}'s use of the \pkg{overcite}. 
Separate reference numbers are shown with
commas\cite{sutton:85ar,miner:75ncr,turner:64a} and ranges are 
separated by an en-dash.\cite{sutton:85ar,miner:75ncr,wirin:90cp}
Reference citations in the text should be in numerical order, which is
assured by using \textsc{Bib}\TeX.

In the reference list, give all authors' names; do not use ``et al.''
unless there are six authors or more.
Papers that have not been published should be cited as ``unpublished'';
papers that have been submitted or accepted for publication should be
cited as ``submitted for publication.''
Private communications and personal Web sites should appear as footnotes
rather than in the reference list.

References should be cited according to the standard publication
reference style.
(For examples, see the ``References'' section of this template.)
This is facilitated by the Bib\TeX\ database and a style file, \file{aiaa.bst}.
As a rule, all words are capitalized except for articles, conjunctions,
and prepositions of four letters or fewer.
Names and locations of publishers should be listed; month and year
should be included for reports and papers.
For papers published in translation journals, please give the English
citation first, followed by the original foreign language citation.

\subsection{Images, Figures, and Tables}

All artwork, captions, figures, graphs, and tables will be reproduced
exactly as submitted.
Be sure to position any figures, tables, graphs, or pictures as you want
them printed.
AIAA is not responsible for incorporating your figures, tables,
etc.%
\footnote{Company logos and identification numbers are not permitted on
  your illustrations.}

% an experiment with wrapfig -- read caveats documented in wrapfig.sty
\begin{wrapfigure}{R}{0.5\linewidth}
 
 \caption{Magnetization as a function of applied field, which has
   borders so thick that they overwhelm the data and for some reason the
   ordinate label is rotated 90 degrees to make it difficult to
   read. This figure also demonstrates the dangers of using a bitmap
   as opposed to a vector image.}
 \label{f:magnetic_field}
\end{wrapfigure}

Place figure captions below all figures; place table titles above the
tables.%
\footnote{Please do not include captions as part of the figure image
itself.}
If your figure has multiple parts, include the labels ``a),'' ``b),''
and so on, below each subfigure and above the figure caption.
This can be accomplished with the \pkg{subfigure} package.
Please verify that the figures and tables you mention in the text
actually exist by using \LaTeX's \verb|\label| and \verb|\ref| mechanisms
and verifying that there are no undefined references during typesetting.

When citing a figure in the text, use ``figure'' as ``Fig., often used
to refer to graphics, is an ugly abbreviation and is not worth the two
spaces saved.''\cite{tufte:83bk}
Do not abbreviate ``table'' either.
Each different type of illustration (i.e., figures, tables, or
images) should be numbered sequentially with relation to other
illustrations of the same type.

Figure axis labels are often a source of confusion.
Use words rather than symbols.
As in the example to the right, write the quantity ``Magnetization''
rather than just ``M.''
Do not enclose units in parenthesis, but rather separate them from the
preceding text by commas.
Do not label axes only with units.
As in figure~\ref{f:magnetic_field}, for example, write ``Magnetization,
A/m'' or ``Magnetization, A m-1,'' not just ``A/m.''
Do not label axes with a ratio of quantities and units.
For example, write ``Temperature, K,'' not ``Temperature/K.''

Multipliers can be especially confusing.
Write ``Magnetization, kA/m'' or ``Magnetization, 103 A/m.''
Do not write ``Magnetization (A/m) $\times$ 1000'' because the reader
would not then know whether the top axis label in
figure~\ref{f:magnetic_field} meant 16000~A/m or 0.016~A/m.
Figure labels must be legible, approximately 8--12 point type.
Use of the \pkg{psfrag} package can facilitate this, but it makes
generating a PDF version of your paper difficult.

Figures and tables are referred to as `Floats' in \LaTeX, reflecting
their floating nature.
They are typically numbered whether or not they have a caption and they
are floated to the first available position near the first reference to
that figure/table within the text.
This is accomplished by placing the figure/table environment after
their first reference.
The environment can even be placed mid-sentence as long as \LaTeX's
comment character, \%, is used properly to prevent a paragraph break or
extra spaces.
By default, floats are placed at the top of the first available page,
the bottom of the page, or one a page consisting entirely of floats.

An example of coding a standard \verb|{figure}| is given below:
\begin{Verbatim}
 \begin{figure}
   
   \caption{Magnetization as a function of applied field, which has
     borders so thick that they overwhelm from the data.}
   \label{f:magnetic_field}
 \end{figure}
\end{Verbatim}

\begin{table}
 \begin{center}
  \begin{threeparttable}
   \caption{This is an example of a \pkg{threeparttable} which uses the
     \pkg{dcolumn} package to allow for columns to be aligned on decimal
     points.}
   \label{t:threepart}
   \begin{tabular}{lcdd}
    First head\tnote{*}  &
    Second head &
    \multicolumn{1}{c}{Third head} &
    \multicolumn{1}{c}{$V_M(r)$} \\\hline
    center & doctor &  0.2  & 10.55 \\  
    tab    & dentist &  0.15 & 33.12 \\ 
    worse  & man\tnote{\ensuremath{\dagger}} & 10.58 & 45.10 \\ 
    better & home & 43.9  & 12.34 \\
   \end{tabular}
   \begin{tablenotes}
    \item[*] This is a table footnote, which to span multiple lines, has
      been greatly extended in length contrary to reason.
    \item[\ensuremath{\dagger}] A much shorter table footnote.
   \end{tablenotes}
  \end{threeparttable}
 \end{center}
\end{table}
Tables with footnotes, such as table~\ref{t:threepart},
can be coded using the \pkg{threeparttable} package as follows:
\begin{Verbatim}
 \begin{table}
  \begin{center}
   \begin{threeparttable}
    \caption{This is an example of table caption.}
    \label{t:wordtable}
    \begin{tabular}{ccdd}
     First head\tnote{a}  &
     Second head\tnote{b} &
     \multicolumn{1}{c}{Third head} &
     \multicolumn{1}{c}{$V_M(r)$} \\\hline
     Left & Word entries &  0.2  & 10.55 \\  
     Left & Word entries &  0.15 & 33.12 \\ 
     Left & Word entries & 10.58 & 45.10 \\ 
     Left & Word entries & 43.9  & 12.34 \\
    \end{tabular}
    \begin{tablenotes}
     \item[a] This is a table footnote, which to span multiple lines, has
              been greatly extended in length contrary to reason.
     \item[b] A much shorter table footnote.
    \end{tablenotes}
   \end{threeparttable}
  \end{center}
 \end{table}
\end{Verbatim}

\subsection{Equations, Numbers, Symbols, and Abbreviations}

Equations are centered and numbered consecutively, with equation
numbers in parentheses flush right, as in Eq.~\ref{e:function}.
\begin{equation}
 \label{e:function}
 \int_{0}^{r_{2}} F(r,\varphi)\,dr\,d\varphi =
    \left[ \sigma r_{2}/(2\mu_{0}) \right] \cdot
    \int_{0}^{\infty} \exp(-\rho|z_{j}-z_{i}|) \lambda^{-1} 
\end{equation}
Equation~\ref{e:function} is coded as below:
\begin{Verbatim}
 \begin{equation}
  \label{e:function}
  \int_{0}^{r_{2}} F(r,\varphi)\,dr\,d\varphi =
     \left[ \sigma r_{2}/(2\mu_{0}) \right] \cdot
     \int_{0}^{\infty} \exp(-\rho|z_{j}-z_{i}|) \lambda^{-1}
 \end{equation}
\end{Verbatim}
A sample equation is included below, formatted using the preceding
instructions.
To make your equation more compact, you can use the solidus ($/$), the
exp function, or appropriate exponents.
Use parentheses to avoid ambiguities in denominators.
\begin{equation}
  \label{e:displace}
  \mathbf{J}_i\cdot\Delta\underline{x}_{i+1}=-\underline{f}_i
\end{equation}
\nomenclature{$J$}{Jacobian Matrix}
\nomenclature[b$i$]{$i$}{Variable number}
\nomenclature[g$\Delta$]{$\Delta x$}{Variable displacement vector}
\nomenclature{$f$}{Residual value vector}
\nomenclature{$x$}{Variable value vector}
\begin{equation}
  \label{e:newton}
  F=m\alpha
\end{equation}
\nomenclature{$F$}{Force, N}
\nomenclature{$m$}{Mass, kg}
\nomenclature[g$\alpha$]{$\alpha$}{Acceleration, m/s\textsuperscript{2}}

The \verb|fleqnarray| environment is used to display a sequence of
equations or inequalities. It is very much like a three-column
\verb|array| environment, with consecutive rows separated by
\verb|\\| and consecutive items within a row separated by an \&.
\begin{eqnarray}
&&\sum_{i\in H} p^0\cdot w^{0i}=\sum_i M^i (p^0) =
  \sum_i\left[p^0\cdot r^i + \sum_j \alpha^{ij} (p^0\cdot
  y^{0j})\right]\nonumber\\
&&{\qquad}= p^0 \cdot \sum_i r^i + p^0 \cdot \sum_i
\sum_i \alpha^{ij}
\end{eqnarray}
An equation number is placed on every line unless that line has a
\verb|\nonumber| command.

Be sure that the symbols in your equation are defined before the
equation appears, or immediately following.
In this case the \pkg{nomencl} package is used to automatically generate
the nomenclature section.

Italicize symbols ($T$ might refer to temperature, but T is the unit
Tesla).
Refer to ``Eq. (1),'' not ``(1)'' or ``equation (1)'' except at the
beginning of a sentence: ``Equation (1) is phat.''
Equations can be labeled other than ``Eq.'' should they represent
inequalities, matrices, or boundary conditions.
If what is represented is really more than one equation, the
abbreviation ``Eqs.'' can be used.

Define abbreviations and acronyms the first time they are used in the
text, even after they have already been defined in the abstract.
Very common abbreviations such as AIAA, SI, ac, and dc do not have to be
defined.
Abbreviations that incorporate periods should not have spaces: write
``P.R.,'' not ``P. R.''
Delete periods between initials if the abbreviation has three or more
initials; e.g., U.N. but ESA.\@
Do not use abbreviations in the title unless they are unavoidable (for
instance, ``AIAA'' in the title of this article).

\subsection{General Grammar and Preferred Usage}

Use only one space after periods or colons. Hyphenate complex
modifiers: ``zero-field-cooled magnetization.''
Avoid dangling participles, such as, ``Using Eq. (1), the potential was
calculated.''
[It is not clear who or what used Eq. (1).]
Write instead ``The potential was calculated using Eq. (1),'' or ``Using
Eq. (1), we calculated the potential.''

Use a zero before decimal points: ``0.25,'' not ``.25.''
Use ``cm$^3$,'' not ``cc.''
Indicate sample dimensions as ``0.1 cm $\times$ 0.2 cm,'' not ``0.1
$\times$ 0.2~cm$^2$.''
The preferred abbreviation for ``seconds'' is ``s,'' not ``sec.''
Do not mix complete spellings and abbreviations of units: use
``Wb/m$^2$'' or ``webers per square meter,'' not ``webers/m$^2$.''
When expressing a range of values, write ``7 to 9'' or ``7--9,'' not
``7~9.''

A parenthetical statement at the end of a sentence is punctuated
outside of the closing parenthesis (like this).
(A parenthetical sentence is punctuated within parenthesis.)
In American English, periods and commas are placed within quotation
marks, like ``this period.''
Other punctuation is ``outside''! Avoid contractions; for example, write
``do not'' instead of ``don't.''
The serial comma is preferred: ``A, B, and C'' instead of ``A, B and C.''

If you wish, you may write in the first person singular or plural and
use the active voice (``I observed that\ldots'' or ``We observed that\ldots''
instead of ``It was observed that…'').
Remember to check spelling.
If your native language is not English, please ask a native
English-speaking colleague to proofread your paper.

The word ``data'' is plural, not singular (i.e., ``data are,'' not ``data
is'').
The subscript for the permeability of vacuum $\mu_0$ is zero, not a
lowercase letter ``oo.''
The term for residual magnetization is ``remanence''; the adjective is
``remanent''; do not write ``remnance'' or ``remnant.''
The word ``micrometer'' is preferred over ``micron'' when spelling out
this unit of measure.
A graph within a graph is an ``inset,'' not an ``insert.''
The word ``alternatively'' is preferred to the word ``alternately''
(unless you really mean something that alternates).
Use the word ``whereas'' instead of ``while'' (unless you are referring
to simultaneous events).
Do not use the word ``essentially'' to mean ``approximately'' or
``effectively.''
Do not use the word ``issue'' as a euphemism for ``problem.''
When compositions are not specified, separate chemical symbols by
en-dashes; for example, ``NiMn'' indicates the intermetallic compound
Ni$_{0.5}$Mn$_{0.5}$ whereas ``Ni--Mn'' indicates an alloy of some
composition Ni$_{x}$Mn$_{1-x}$.

Be aware of the different meanings of the homophones ``affect'' (usually
a verb) and ``effect'' (usually a noun), ``complement'' and
``compliment,'' ``discreet'' and ``discrete,'' ``principal'' (e.g.,
``principal investigator'') and ``principle'' (e.g., ``principle of
measurement''). Do not confuse ``imply'' and ``infer.''

Prefixes such as ``non,'' ``sub,'' ``micro,'' ``multi,'' and ``ultra''
are not independent words; they should be joined to the words they
modify, usually without a hyphen.
There is no period after the ``et'' in the abbreviation ``et al.''
The abbreviation ``i.e.,'' means ``that is,'' and the abbreviation
``e.g.,'' means ``for example'' (these abbreviations are not
italicized).
An excellent source of more detailed style and formatting instructions
can be found in the AIAA style guide, {\it AIAA Style} (available from AIAA
upon request).

\section{Conclusion}

A conclusion section is not required, though it is preferred.
Although a conclusion may review the main points of the paper, do not
replicate the abstract as the conclusion.
A conclusion might elaborate on the importance of the work or suggest
applications and extensions.%
\footnote{The conclusion section is the last section of
  the paper that should be numbered.
  The appendix (if present), acknowledgment, and references should be
  listed without numbers.}

\section*{Appendix}

An appendix, if needed, should appear before the acknowledgments.
Use the 'starred' version of the \verb|\section| commands to avoid
section numbering.

\section*{Acknowledgments}

The preferred spelling of the word ``acknowledgment'' in American
English is without the ``e'' after the ``g.''
Avoid expressions such as ``One of us (S.B.A.) would like to thank\ldots[.]''
Instead, write ``F. A. Author thanks\ldots[.]''
Sponsor and financial support acknowledgments are also to be listed in
the acknowledgments section.

% produces the bibliography section when processed by BibTeX
\bibliography{bibtex_database}
\bibliographystyle{aiaa}

\end{document}

% $Id: author_guide.tex,v 1.4 2004/05/23 12:49:44 kleb Exp $

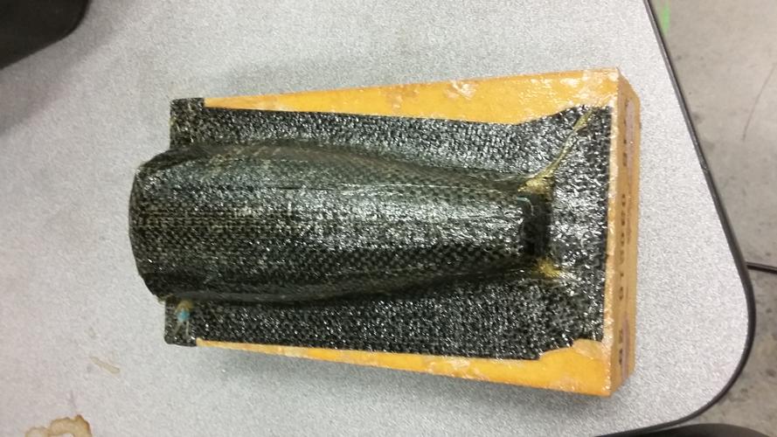
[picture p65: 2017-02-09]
doc/img/tinyTestMold_afterFabrication.jpg

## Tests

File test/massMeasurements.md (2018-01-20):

## Airframe CoM Measurements
Measurements taken on 2018-01-19 with a tolerance of +/- 0.125".
Lengthwise CoMs were determined by the following.
- A 1" diameter HDPE bar stock was taped to a table. 
- A yard stick was placed on the table. 
- The center of the bar stock was aligned to the 20" mark, with the bar stock perpendicular to the yard stick),
- The flight article was placed on the bar stock and adjusted until it balanced freely. (Gentle touches were necessary to stabilize it.)
- A suitable feature was sighted along the yard stick and its distance from the bar stock was recorded.

- PSAS-0001-0006 (standard 18"): 518 g, 9" from the male face
- PSAS-0001-0005 (dragonscale 24"): 703 g, 12.375" from the male face
- PSAS-0001-0015 fin can: 1933 g, 13.875" from the male face
- PSAS-0001-0023 (24" sled module): 707 g, 12.5" from the male face
- PSAS-0001-0004 (standard 24"): 677 g, 18.25" from the male face
- PSAS-0001-0003 (18" radome): 484 g, 9.375" from the male face
- PSAS-0001-0001 (nosecone with tip, rod, and hook): 1394 g, 18.875" from the female skirt
- PSAS-0001-0001 (nosecone alone): 1166 g, 15" from female skirt
- threaded rod: 105 g, 4" long (sits 2.57" out from the skirt of the tip)
- PSAS-0001-0011 (nosecone tip): 122 g
- cradle
	- wood frame: 227 g
	- SLA mount 59 g
	- acrylic spacer: 72 g
	- 6061 mount: 136 g
- dented thrust flange: 79 g
- nice thrust flange: 79 g

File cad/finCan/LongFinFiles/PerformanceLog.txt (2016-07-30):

Mesh Preparation:  0 hr 0 min 0 sec
Standard solid mesh bolt head imprint and hard point processing:  0 hr 0 min 0 sec
Standard solid mesh total preparation including imprint:  0 hr 0 min 1 sec
Standard surface meshing for Solid Mesh:  0 hr 0 min 1 sec
Standard volume meshing for Solid Mesh:  0 hr 0 min 1 sec
Standard solid mesh arranging data:  0 hr 0 min 0 sec
Standard solid mesh total:  0 hr 0 min 3 sec
Beam mesh:  0 hr 0 min 0 sec
Mesh Preparation:  0 hr 0 min 0 sec
Standard solid mesh bolt head imprint and hard point processing:  0 hr 0 min 0 sec
Standard solid mesh total preparation including imprint:  0 hr 0 min 0 sec
Standard surface meshing for Solid Mesh:  0 hr 0 min 1 sec
Standard volume meshing for Solid Mesh:  0 hr 0 min 2 sec
Standard solid mesh arranging data:  0 hr 0 min 0 sec
Standard solid mesh total:  0 hr 0 min 3 sec
Beam mesh:  0 hr 0 min 0 sec
Preparing to transfer data:  0 hr 0 min 0 sec
Processing material properties:  0 hr 0 min 0 sec
Processing element groups:  0 hr 0 min 0 sec
Processing drop test gap nodes:  0 hr 0 min 0 sec
Updating thickness for shell regions:  0 hr 0 min 0 sec
Processing rconst for elements:  0 hr 0 min 0 sec
Processing egroups:  0 hr 0 min 0 sec
Transferring loads and boundary conditions:  0 hr 0 min 0 sec
Generating contacts:  0 hr 0 min 0 sec
Number of Contacts: 0
Transfer SL1 data:  0 hr 0 min 0 sec
Generate more accurate contact data:  0 hr 0 min 0 sec
Number of contact data: 0
Transfer beam/joint contact data:  0 hr 0 min 0 sec
Transferring other special loads:  0 hr 0 min 0 sec
Transferring bearing loads:  0 hr 0 min 0 sec
Transferring mass elements:  0 hr 0 min 0 sec
Transferring point loads:  0 hr 0 min 0 sec
Transferring distributed beam loads:  0 hr 0 min 0 sec
Transferring rigid bodies:  0 hr 0 min 0 sec
Writing Data:  0 hr 0 min 0 sec
Transferring analysis options:  0 hr 0 min 0 sec
Total midsurf mapping:  0 hr 0 min 0 sec

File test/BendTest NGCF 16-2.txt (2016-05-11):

NI VI Logger                            
Created: 4/29/2016 12:27:01.621 PM Pacific Daylight Time
Number of scans: 2704
Scan rate: 0.2 seconds

Row,Time,Voltage_0(Voltage),Voltage_1(Voltage),Voltage_2(Voltage),Voltage_3(Voltage)
1,12:15:26.421 PM,0.00421669,2.0887,-0.00203558,-0.280847
2,12:15:26.621 PM,0.00116415,2.0887,-0.00101962,-0.267838
3,12:15:26.821 PM,0.00116415,2.0887,-0.00203558,-0.215804
4,12:15:27.021 PM,0.00218166,2.0887,-0.00203558,-0.25483
5,12:15:27.221 PM,0.00218166,2.0887,-0.00203558,-0.241821
6,12:15:27.421 PM,0.00218166,2.0887,-0.00101962,-0.202795
7,12:15:27.621 PM,0.00319918,2.0887,-0.00101962,-0.241821
8,12:15:27.821 PM,0.00218166,2.0887,-0.00101962,-0.280847
9,12:15:28.021 PM,0.00218166,2.0887,-0.00101962,-0.241821
10,12:15:28.221 PM,0.00218166,2.0887,-0.00101962,-0.241821
11,12:15:28.421 PM,0.00218166,2.0887,-0.00101962,-0.293856
12,12:15:28.621 PM,0.00218166,2.0887,-0.00101962,-0.280847
13,12:15:28.821 PM,0.00218166,2.0887,-0.00101962,-0.228812
14,12:15:29.021 PM,0.00218166,2.0887,-0.00101962,-0.228812
15,12:15:29.221 PM,0.00218166,2.0887,-0.00203558,-0.241821
16,12:15:29.421 PM,0.00218166,2.0887,-0.00203558,-0.215804
17,12:15:29.621 PM,0.00218166,2.0887,-0.00203558,-0.25483
18,12:15:29.821 PM,0.00319918,2.0887,-0.00203558,-0.25483
19,12:15:30.021 PM,0.00218166,2.0887,-0.00203558,-0.280847
20,12:15:30.221 PM,0.00218166,2.0887,-0.00203558,-0.280847
21,12:15:30.421 PM,0.00218166,2.0887,-0.00203558,-0.228812
22,12:15:30.621 PM,0.00116415,2.0887,-0.00101962,-0.267838
23,12:15:30.821 PM,0.00218166,2.0887,-0.00101962,-0.267838
24,12:15:31.021 PM,0.00116415,2.0887,-0.00203558,-0.215804
25,12:15:31.221 PM,0.00218166,2.0887,-0.00203558,-0.228812
26,12:15:31.421 PM,0.00218166,2.0887,-0.00101962,-0.267838
27,12:15:31.621 PM,0.00218166,2.0887,-0.00203558,-0.280847
28,12:15:31.821 PM,0.00218166,2.0887,-0.00101962,-0.319873
29,12:15:32.021 PM,0.00218166,2.0887,-0.00203558,-0.293856
30,12:15:32.221 PM,0.00218166,2.0887,-0.00101962,-0.267838
31,12:15:32.421 PM,0.00116415,2.0887,-0.00101962,-0.267838
32,12:15:32.621 PM,0.00218166,2.0887,-0.00203558,-0.280847
33,12:15:32.821 PM,0.00218166,2.0887,-0.00203558,-0.280847
34,12:15:33.021 PM,0.00116415,2.0887,-0.00203558,-0.280847
35,12:15:33.221 PM,0.00218166,2.0887,-0.00101962,-0.215804
36,12:15:33.421 PM,0.00218166,2.0887,-0.00203558,-0.241821
37,12:15:33.621 PM,0.00319918,2.0887,-0.00101962,-0.241821
38,12:15:33.821 PM,0.00319918,2.0887,-0.00101962,-0.267838
39,12:15:34.021 PM,0.00421669,2.0887,-0.00101962,-0.215804
40,12:15:34.221 PM,0.00421669,2.0887,-0.00101962,-0.280847
41,12:15:34.421 PM,0.00421669,2.0887,-0.00203558,-0.25483
42,12:15:34.621 PM,0.00421669,2.0887,-0.00101962,-0.25483
43,12:15:34.821 PM,0.00421669,2.0887,-0.00203558,-0.267838
44,12:15:35.021 PM,0.00421669,2.0887,-3.66674E-6,-0.215804
45,12:15:35.221 PM,0.0052342,2.0887,-0.00203558,-0.228812
46,12:15:35.421 PM,0.00421669,2.0887,-0.00203558,-0.241821
47,12:15:35.621 PM,0.00319918,2.0887,-0.00203558,-0.241821
48,12:15:35.821 PM,0.00319918,2.0887,-0.00101962,-0.280847
49,12:15:36.021 PM,0.00319918,2.0887,-0.00203558,-0.280847
50,12:15:36.221 PM,0.00218166,2.0887,-0.00101962,-0.215804
51,12:15:36.421 PM,0.00116415,2.0887,-0.00101962,-0.267838
52,12:15:36.621 PM,0.00116415,2.0887,-0.00203558,-0.280847
53,12:15:36.821 PM,0.00116415,2.0887,-0.00101962,-0.280847
54,12:15:37.021 PM,0.00218166,2.0887,-0.00101962,-0.267838
55,12:15:37.221 PM,0.00116415,2.0887,-0.00101962,-0.280847
56,12:15:37.421 PM,0.00116415,2.0887,-0.00101962,-0.228812
57,12:15:37.621 PM,0.00218166,2.0887,-0.00101962,-0.25483
58,12:15:37.821 PM,0.00116415,2.0887,-0.00101962,-0.241821
59,12:15:38.021 PM,0.00116415,2.0887,-0.00203558,-0.241821
60,12:15:38.221 PM,0.00116415,2.0887,-0.00101962,-0.25483
61,12:15:38.421 PM,0.000146639,2.0887,-0.00203558,-0.189786
62,12:15:38.621 PM,0.000146639,2.0887,-0.00203558,-0.267838
63,12:15:38.821 PM,0.00116415,2.0887,-0.00101962,-0.25483
64,12:15:39.021 PM,0.000146639,2.0887,-0.00203558,-0.215804
65,12:15:39.221 PM,0.000146639,2.0887,-0.00101962,-0.25483
66,12:15:39.421 PM,0.000146639,2.0887,-0.00203558,-0.306865
67,12:15:39.621 PM,-0.00188839,2.0887,-0.00203558,-0.267838
68,12:15:39.821 PM,0.000146639,2.0887,-0.00203558,-0.241821
69,12:15:40.021 PM,-0.000870874,2.0887,-0.00203558,-0.241821
70,12:15:40.221 PM,0.000146639,2.0887,-0.00101962,-0.267838
71,12:15:40.421 PM,-0.000870874,2.0887,-0.00101962,-0.306865
72,12:15:40.621 PM,0.000146639,2.0887,-0.00101962,-0.293856
73,12:15:40.821 PM,-0.000870874,2.0887,-0.00203558,-0.267838
74,12:15:41.021 PM,-0.000870874,2.0887,-0.00203558,-0.228812
75,12:15:41.221 PM,-0.000870874,2.0887,-0.00203558,-0.280847
76,12:15:41.421 PM,-0.00188839,2.0887,-0.00203558,-0.241821
77,12:15:41.621 PM,-0.000870874,2.0887,-0.00101962,-0.267838
78,12:15:41.821 PM,-0.0029059,2.0887,-0.00101962,-0.280847
79,12:15:42.021 PM,-0.0029059,2.0887,-0.00203558,-0.280847
80,12:15:42.221 PM,-0.00188839,2.0887,-0.00101962,-0.25483
81,12:15:42.421 PM,-0.00188839,2.0887,-0.00203558,-0.280847
82,12:15:42.621 PM,-0.0029059,2.0887,-0.00203558,-0.332882
83,12:15:42.821 PM,-0.00188839,2.0887,-0.00203558,-0.293856
84,12:15:43.021 PM,-0.00188839,2.0887,-0.00101962,-0.358899
85,12:15:43.221 PM,-0.000870874,2.0887,-0.00203558,-0.319873
86,12:15:43.421 PM,-0.00188839,2.0887,-0.00203558,-0.319873
87,12:15:43.621 PM,-0.00188839,2.0887,-0.00203558,-0.319873
88,12:15:43.821 PM,-0.00188839,2.0887,-0.00203558,-0.280847
89,12:15:44.021 PM,-0.00188839,2.0887,-0.00203558,-0.319873
90,12:15:44.221 PM,-0.00188839,2.0887,-0.00101962,-0.319873
91,12:15:44.421 PM,-0.00188839,2.0887,-0.00101962,-0.345891
92,12:15:44.621 PM,-0.00188839,2.0887,-0.00101962,-0.332882
93,12:15:44.821 PM,-0.00188839,2.0887,-3.66674E-6,-0.332882
94,12:15:45.021 PM,-0.0029059,2.0887,-0.00203558,-0.332882
95,12:15:45.221 PM,-0.00188839,2.0887,-0.00203558,-0.280847
96,12:15:45.421 PM,-0.0029059,2.0887,-0.00203558,-0.397925
97,12:15:45.621 PM,-0.00188839,2.0887,-0.00101962,-0.397925
98,12:15:45.821 PM,-0.00188839,2.0887,-0.00203558,-0.345891
99,12:15:46.021 PM,-0.0029059,2.0887,-0.00101962,-0.319873
100,12:15:46.221 PM,-0.000870874,2.0887,-0.00101962,-0.345891
101,12:15:46.421 PM,-0.000870874,2.0887,-0.00203558,-0.306865
102,12:15:46.621 PM,-0.0029059,2.0887,-0.00203558,-0.423943
103,12:15:46.821 PM,-0.00188839,2.0887,-0.00203558,-0.345891
104,12:15:47.021 PM,-0.000870874,2.0887,-0.00203558,-0.332882
105,12:15:47.221 PM,-0.0029059,2.0887,-3.66674E-6,-0.280847
106,12:15:47.421 PM,-0.0029059,2.0887,-0.00203558,-0.371908
107,12:15:47.621 PM,-0.0029059,2.0887,-0.00101962,-0.280847
108,12:15:47.821 PM,-0.00188839,2.0887,-0.00203558,-0.280847
109,12:15:48.021 PM,-0.00188839,2.0887,-0.00101962,-0.319873
110,12:15:48.221 PM,-0.0029059,2.0887,-0.00203558,-0.332882
111,12:15:48.421 PM,-0.00188839,2.0887,-0.00203558,-0.267838
112,12:15:48.621 PM,-0.000870874,2.0887,-0.00203558,-0.306865
113,12:15:48.821 PM,-0.000870874,2.0887,-0.00101962,-0.306865
114,12:15:49.021 PM,-0.0029059,2.0887,-0.00101962,-0.319873
115,12:15:49.221 PM,-0.00188839,2.0887,-0.00203558,-0.306865
116,12:15:49.421 PM,-0.00188839,2.0887,-0.00203558,-0.332882
117,12:15:49.621 PM,-0.00188839,2.0887,-0.00101962,-0.358899
118,12:15:49.821 PM,-0.00392341,2.0887,-0.00203558,-0.267838
119,12:15:50.021 PM,-0.00188839,2.0887,-0.00101962,-0.306865
120,12:15:50.221 PM,-0.00188839,2.0887,-0.00203558,-0.293856
121,12:15:50.421 PM,-0.000870874,2.0887,-0.00101962,-0.384917
122,12:15:50.621 PM,-0.0029059,2.0887,-0.00203558,-0.371908
123,12:15:50.821 PM,-0.00188839,2.0887,-0.00101962,-0.371908
124,12:15:51.021 PM,-0.00188839,2.0887,-0.00101962,-0.319873
125,12:15:51.221 PM,-0.00188839,2.0887,-0.00101962,-0.241821
126,12:15:51.421 PM,-0.00188839,2.0887,-0.00101962,-0.293856
127,12:15:51.621 PM,-0.00188839,2.0887,-0.00203558,-0.306865
128,12:15:51.821 PM,-0.00188839,2.0887,-0.00101962,-0.280847
129,12:15:52.021 PM,-0.00188839,2.0887,-0.00203558,-0.280847
130,12:15:52.221 PM,-0.00188839,2.0887,-0.00101962,-0.228812
131,12:15:52.421 PM,-0.00188839,2.0887,-0.00101962,-0.280847
132,12:15:52.621 PM,-0.0029059,2.0887,-0.00203558,-0.280847
133,12:15:52.821 PM,-0.00188839,2.0887,-0.00101962,-0.241821
134,12:15:53.021 PM,-0.00188839,2.0887,-0.00101962,-0.241821
135,12:15:53.221 PM,-0.00188839,2.0887,-0.00203558,-0.228812
136,12:15:53.421 PM,-0.0029059,2.0887,-0.00101962,-0.202795
137,12:15:53.621 PM,-0.00188839,2.0887,-0.00101962,-0.202795
138,12:15:53.821 PM,-0.00188839,2.0887,-0.00203558,-0.228812
139,12:15:54.021 PM,-0.00188839,2.0887,-0.00203558,-0.25483
140,12:15:54.221 PM,-0.0029059,2.0887,-0.00101962,-0.228812
141,12:15:54.421 PM,-0.00188839,2.0887,-0.00101962,-0.176778
142,12:15:54.621 PM,-0.0029059,2.0887,-0.00203558,-0.202795
143,12:15:54.821 PM,-0.0029059,2.0887,-0.00203558,-0.202795
144,12:15:55.021 PM,-0.000870874,2.0887,-0.00101962,-0.189786
145,12:15:55.221 PM,-0.000870874,2.0887,-0.00203558,-0.215804
146,12:15:55.421 PM,-0.00188839,2.0887,-0.00203558,-0.163769
147,12:15:55.621 PM,-0.00188839,2.0887,-0.00101962,-0.228812
148,12:15:55.821 PM,-0.0029059,2.0887,-0.00101962,-0.176778
149,12:15:56.021 PM,-0.00188839,2.0887,-0.00101962,-0.215804
150,12:15:56.221 PM,-0.00188839,2.0887,-0.00203558,-0.215804
151,12:15:56.421 PM,-0.00188839,2.0887,-0.00101962,-0.241821
152,12:15:56.621 PM,-0.00188839,2.0887,-0.00101962,-0.215804
153,12:15:56.821 PM,-0.00188839,2.0887,-0.00101962,-0.189786
154,12:15:57.021 PM,-0.00188839,2.0887,-0.00203558,-0.215804
155,12:15:57.221 PM,-0.00188839,2.0887,-0.00203558,-0.163769
156,12:15:57.421 PM,-0.0029059,2.0887,-0.00101962,-0.241821
157,12:15:57.621 PM,-0.00188839,2.0887,-0.00101962,-0.176778
158,12:15:57.821 PM,-0.00188839,2.0887,-0.00101962,-0.176778
159,12:15:58.021 PM,-0.000870874,2.0887,-0.00203558,-0.267838
160,12:15:58.221 PM,-0.000870874,2.0887,-0.00203558,-0.228812
161,12:15:58.421 PM,-0.00188839,2.0887,-0.00203558,-0.241821
162,12:15:58.621 PM,-0.0029059,2.0887,-0.00203558,-0.202795
163,12:15:58.821 PM,-0.0029059,2.0887,-0.00203558,-0.202795
164,12:15:59.021 PM,-0.00188839,2.0887,-0.00203558,-0.202795
165,12:15:59.221 PM,-0.00188839,2.0887,-0.00203558,-0.228812
166,12:15:59.421 PM,-0.00188839,2.0887,-0.00203558,-0.176778
167,12:15:59.621 PM,-0.00188839,2.0887,-0.00203558,-0.176778
168,12:15:59.821 PM,-0.00188839,2.0887,-0.00203558,-0.124743
169,12:16:00.021 PM,-0.0029059,2.0887,-0.00101962,-0.189786
170,12:16:00.221 PM,-0.00188839,2.0887,-0.00101962,-0.202795
171,12:16:00.421 PM,-0.000870874,2.0887,-0.00203558,-0.241821
172,12:16:00.621 PM,-0.0029059,2.0887,-0.00101962,-0.228812
173,12:16:00.821 PM,-0.00188839,2.0887,-0.00203558,-0.25483
174,12:16:01.021 PM,-0.00188839,2.0887,-0.00203558,-0.202795
175,12:16:01.221 PM,-0.00188839,2.0887,-0.00203558,-0.228812
176,12:16:01.421 PM,-0.00188839,2.0887,-0.00101962,-0.241821
177,12:16:01.621 PM,-0.0029059,2.0887,-0.00203558,-0.319873
178,12:16:01.821 PM,-0.00188839,2.0887,-0.00101962,-0.25483
179,12:16:02.021 PM,-0.0029059,2.0887,-0.00101962,-0.280847
180,12:16:02.221 PM,-0.00188839,2.0887,-0.00203558,-0.280847
181,12:16:02.421 PM,-0.0029059,2.0887,-0.00203558,-0.267838
182,12:16:02.621 PM,-0.00188839,2.0887,-0.00203558,-0.280847
183,12:16:02.821 PM,-0.00188839,2.0887,-0.00203558,-0.267838
184,12:16:03.021 PM,-0.0029059,2.0887,-0.00203558,-0.280847
185,12:16:03.221 PM,-0.000870874,2.0887,-0.00203558,-0.241821
186,12:16:03.421 PM,-0.00188839,2.0887,-0.00203558,-0.306865
187,12:16:03.621 PM,-0.00188839,2.0887,-0.00203558,-0.25483
188,12:16:03.821 PM,-0.000870874,2.0887,-0.00101962,-0.215804
189,12:16:04.021 PM,-0.00188839,2.0887,-0.00101962,-0.280847
190,12:16:04.221 PM,-0.0029059,2.0887,-0.00203558,-0.228812
191,12:16:04.421 PM,-0.000870874,2.0887,-0.00101962,-0.267838
192,12:16:04.621 PM,-0.00188839,2.0887,-0.00101962,-0.241821
193,12:16:04.821 PM,-0.00188839,2.0887,-3.66674E-6,-0.241821
194,12:16:05.021 PM,-0.0029059,2.0887,-0.00203558,-0.228812
195,12:16:05.221 PM,-0.00188839,2.0887,-0.00101962,-0.215804
196,12:16:05.421 PM,-0.00188839,2.0887,-0.00203558,-0.215804
197,12:16:05.621 PM,-0.00188839,2.0887,-0.00101962,-0.215804
198,12:16:05.821 PM,-0.00188839,2.0887,-0.00101962,-0.202795
199,12:16:06.021 PM,-0.00188839,2.0887,-0.00101962,-0.215804
200,12:16:06.221 PM,-0.00188839,2.0887,-0.00101962,-0.267838
201,12:16:06.421 PM,-0.00188839,2.0887,-0.00203558,-0.280847
202,12:16:06.621 PM,-0.00188839,2.0887,-0.00203558,-0.319873
203,12:16:06.821 PM,-0.0029059,2.0887,-0.00203558,-0.306865
204,12:16:07.021 PM,-0.00188839,2.0887,-0.00101962,-0.267838
205,12:16:07.221 PM,-0.0029059,2.0887,-0.00101962,-0.267838
206,12:16:07.421 PM,-0.00188839,2.0887,-0.00101962,-0.293856
207,12:16:07.621 PM,-0.00188839,2.0887,-0.00203558,-0.293856
208,12:16:07.821 PM,-0.00188839,2.0887,-0.00203558,-0.267838
209,12:16:08.021 PM,-0.00188839,2.0887,-0.00101962,-0.267838
210,12:16:08.221 PM,-0.00188839,2.0887,-0.00101962,-0.306865
211,12:16:08.421 PM,-0.0029059,2.0887,-0.00203558,-0.267838
212,12:16:08.621 PM,-0.00188839,2.0887,-0.00101962,-0.241821
213,12:16:08.821 PM,-0.0029059,2.0887,-0.00203558,-0.280847
214,12:16:09.021 PM,-0.000870874,2.0887,-0.00101962,-0.280847
215,12:16:09.221 PM,-0.00188839,2.0887,-0.00203558,-0.280847
216,12:16:09.421 PM,-0.0029059,2.0887,-0.00101962,-0.25483
217,12:16:09.621 PM,-0.00188839,2.0887,-0.00203558,-0.241821
218,12:16:09.821 PM,-0.00188839,2.0887,-0.00203558,-0.267838
219,12:16:10.021 PM,-0.0029059,2.0887,-0.00203558,-0.25483
220,12:16:10.221 PM,-0.00188839,2.0887,-3.66674E-6,-0.319873
221,12:16:10.421 PM,-0.0029059,2.0887,-0.00203558,-0.280847
222,12:16:10.621 PM,-0.0029059,2.0887,-0.00101962,-0.306865
223,12:16:10.821 PM,-0.00188839,2.0887,-0.00101962,-0.319873
224,12:16:11.021 PM,-0.0029059,2.0887,-0.00203558,-0.25483
225,12:16:11.221 PM,-0.00188839,2.0887,-0.00101962,-0.228812
226,12:16:11.421 PM,-0.000870874,2.0887,-0.00101962,-0.267838
227,12:16:11.621 PM,-0.00188839,2.0887,-0.00203558,-0.25483
228,12:16:11.821 PM,-0.00188839,2.0887,-0.00203558,-0.267838
229,12:16:12.021 PM,-0.00188839,2.0887,-0.00101962,-0.306865
230,12:16:12.221 PM,-0.000870874,2.0887,-0.00203558,-0.267838
231,12:16:12.421 PM,-0.00188839,2.0887,-0.00101962,-0.215804
232,12:16:12.621 PM,-0.00188839,2.0887,-0.00101962,-0.202795
233,12:16:12.821 PM,-0.0029059,2.0887,-0.00101962,-0.189786
234,12:16:13.021 PM,-0.000870874,2.0887,-0.00101962,-0.241821
235,12:16:13.221 PM,-0.0029059,2.0887,-0.00101962,-0.189786
236,12:16:13.421 PM,-0.00188839,2.0887,-0.00101962,-0.215804
237,12:16:13.621 PM,-0.00188839,2.0887,-0.00101962,-0.202795
238,12:16:13.821 PM,-0.00188839,2.0887,-0.00203558,-0.306865
239,12:16:14.021 PM,-0.0029059,2.0887,-0.00101962,-0.358899
240,12:16:14.221 PM,-0.00188839,2.0887,-0.00101962,-0.410934
241,12:16:14.421 PM,-0.0029059,2.0887,-0.00101962,-0.280847
242,12:16:14.621 PM,-0.0029059,2.0887,-0.00203558,-0.202795
243,12:16:14.821 PM,-0.0029059,2.0887,-0.00101962,-0.241821
244,12:16:15.021 PM,-0.00188839,2.0887,-0.00203558,-0.215804
245,12:16:15.221 PM,-0.0029059,2.0887,-0.00203558,-0.25483
246,12:16:15.421 PM,-0.0029059,2.0887,-0.00101962,-0.241821
247,12:16:15.621 PM,-0.0029059,2.0887,-0.00203558,-0.241821
248,12:16:15.821 PM,-0.0029059,2.0887,-0.00203558,-0.280847
249,12:16:16.021 PM,-0.0029059,2.0887,-0.00203558,-0.25483
250,12:16:16.221 PM,-0.00188839,2.0887,-0.00203558,-0.241821
251,12:16:16.421 PM,-0.0029059,2.0887,-0.00203558,-0.306865
252,12:16:16.621 PM,-0.0029059,2.0887,-0.00101962,-0.25483
253,12:16:16.821 PM,-0.00188839,2.0887,-0.00203558,-0.228812
254,12:16:17.021 PM,-0.00188839,2.0887,-0.00203558,-0.293856
255,12:16:17.221 PM,-0.0029059,2.0887,-0.00101962,-0.306865
256,12:16:17.421 PM,-0.00188839,2.0887,-0.00101962,-0.345891
257,12:16:17.621 PM,-0.0029059,2.0887,-0.00203558,-0.267838
258,12:16:17.821 PM,-0.00188839,2.0887,-0.00101962,-0.241821
259,12:16:18.021 PM,-0.0029059,2.0887,-0.00203558,-0.293856
260,12:16:18.221 PM,-0.0029059,2.0887,-0.00203558,-0.25483
261,12:16:18.421 PM,-0.0029059,2.0887,-0.00203558,-0.215804
262,12:16:18.621 PM,-0.0029059,2.0887,-0.00203558,-0.25483
263,12:16:18.821 PM,-0.00188839,2.0887,-0.00101962,-0.241821
264,12:16:19.021 PM,-0.000870874,2.0887,-0.00101962,-0.306865
265,12:16:19.221 PM,-0.00188839,2.0887,-0.00203558,-0.319873
266,12:16:19.421 PM,-0.00188839,2.0887,-0.00101962,-0.25483
267,12:16:19.621 PM,-0.00188839,2.0887,-0.00101962,-0.228812
268,12:16:19.821 PM,-0.00188839,2.0887,-0.00203558,-0.25483
269,12:16:20.021 PM,-0.0029059,2.0887,-0.00101962,-0.25483
270,12:16:20.221 PM,-0.00188839,2.0887,-0.00101962,-0.267838
271,12:16:20.421 PM,-0.00188839,2.0887,-0.00101962,-0.306865
272,12:16:20.621 PM,-0.0029059,2.0887,-0.00203558,-0.319873
273,12:16:20.821 PM,-0.0029059,2.0887,-0.00203558,-0.293856
274,12:16:21.021 PM,-0.00188839,2.0887,-0.00101962,-0.241821
275,12:16:21.221 PM,-0.000870874,2.0887,-0.00203558,-0.293856
276,12:16:21.421 PM,-0.00188839,2.0887,-0.00203558,-0.241821
277,12:16:21.621 PM,-0.0029059,2.0887,-0.00101962,-0.241821
278,12:16:21.821 PM,-0.00188839,2.0887,-0.00203558,-0.189786
279,12:16:22.021 PM,-0.00188839,2.0887,-0.00101962,-0.241821
280,12:16:22.221 PM,-0.0029059,2.0887,-0.00101962,-0.306865
281,12:16:22.421 PM,-0.00188839,2.0887,-0.00203558,-0.306865
282,12:16:22.621 PM,-0.00188839,2.0887,-0.00101962,-0.280847
283,12:16:22.821 PM,-0.00188839,2.0887,-0.00203558,-0.215804
284,12:16:23.021 PM,-0.000870874,2.0887,-0.00203558,-0.228812
285,12:16:23.221 PM,-0.000870874,2.0887,-0.00203558,-0.228812
286,12:16:23.421 PM,0.000146639,2.0887,-0.00101962,-0.280847
287,12:16:23.621 PM,0.000146639,2.0887,-0.00203558,-0.202795
288,12:16:23.821 PM,0.000146639,2.0887,-0.00203558,-0.176778
289,12:16:24.021 PM,0.000146639,2.0887,-0.00203558,-0.215804
290,12:16:24.221 PM,0.000146639,2.0887,-0.00101962,-0.163769
291,12:16:24.421 PM,0.00218166,2.0887,-0.00101962,-0.176778
292,12:16:24.621 PM,0.00218166,2.0887,-0.00101962,-0.215804
293,12:16:24.821 PM,0.00319918,2.0887,-0.00101962,-0.25483
294,12:16:25.021 PM,0.0052342,2.0887,-0.00101962,-0.280847
295,12:16:25.221 PM,0.00421669,2.0887,-0.00203558,-0.202795
296,12:16:25.421 PM,0.00625172,2.0887,-0.00203558,-0.280847
297,12:16:25.621 PM,0.00726923,2.0887,-0.00101962,-0.267838
298,12:16:25.821 PM,0.00726923,2.0887,-0.00101962,-0.189786
299,12:16:26.021 PM,0.00828674,2.0887,-0.00203558,-0.228812
300,12:16:26.221 PM,0.00828674,2.0887,-0.00203558,-0.25483
301,12:16:26.421 PM,0.00828674,2.0887,-0.00101962,-0.202795
302,12:16:26.621 PM,0.00930425,2.0887,-0.00203558,-0.176778
303,12:16:26.821 PM,0.00828674,2.0887,-0.00203558,-0.15076
304,12:16:27.021 PM,0.00930425,2.0887,-0.00101962,-0.202795
305,12:16:27.221 PM,0.00930425,2.0887,-0.00203558,-0.163769
306,12:16:27.421 PM,0.0103218,2.0887,-0.00101962,-0.189786
307,12:16:27.621 PM,0.00930425,2.0887,-0.00101962,-0.202795
308,12:16:27.821 PM,0.0103218,2.0887,-0.00203558,-0.137751
309,12:16:28.021 PM,0.00930425,2.0887,-0.00203558,-0.0857167
310,12:16:28.221 PM,0.0113393,2.0887,-0.00203558,-0.15076
311,12:16:28.421 PM,0.0103218,2.0887,-0.00101962,-0.163769
312,12:16:28.621 PM,0.0113393,2.0887,-0.00203558,-0.189786
313,12:16:28.821 PM,0.0103218,2.0887,-0.00101962,-0.215804
314,12:16:29.021 PM,0.0113393,2.0887,-0.00101962,-0.280847
315,12:16:29.221 PM,0.0113393,2.0887,-0.00101962,-0.189786
316,12:16:29.421 PM,0.0123568,2.0887,-0.00203558,-0.241821
317,12:16:29.621 PM,0.0123568,2.0887,-0.00203558,-0.241821
318,12:16:29.821 PM,0.0113393,2.0887,-0.00101962,-0.293856
319,12:16:30.021 PM,0.0123568,2.0887,-0.00203558,-0.293856
320,12:16:30.221 PM,0.0113393,2.0887,-0.00203558,-0.267838
321,12:16:30.421 PM,0.0123568,2.0887,-0.00203558,-0.25483
322,12:16:30.621 PM,0.0123568,2.0887,-0.00101962,-0.25483
323,12:16:30.821 PM,0.0123568,2.0887,-0.00101962,-0.25483
324,12:16:31.021 PM,0.0123568,2.0887,-0.00101962,-0.15076
325,12:16:31.221 PM,0.0123568,2.0887,-0.00203558,-0.176778
326,12:16:31.421 PM,0.0123568,2.0887,-0.00101962,-0.163769
327,12:16:31.621 PM,0.0123568,2.0887,-0.00203558,-0.15076
328,12:16:31.821 PM,0.0123568,2.0887,-0.00203558,-0.215804
329,12:16:32.021 PM,0.0113393,2.0887,-0.00101962,-0.111734
330,12:16:32.221 PM,0.0123568,2.0887,-0.00203558,-0.124743
331,12:16:32.421 PM,0.0123568,2.0887,-0.00203558,-0.0987254
332,12:16:32.621 PM,0.0123568,2.0887,-0.00203558,-0.189786
333,12:16:32.821 PM,0.0123568,2.0887,-0.00203558,-0.124743
334,12:16:33.021 PM,0.0123568,2.0887,-0.00101962,-0.111734
335,12:16:33.221 PM,0.0123568,2.0887,-0.00203558,-0.137751
336,12:16:33.421 PM,0.0133743,2.0887,-0.00101962,-0.163769
337,12:16:33.621 PM,0.0133743,2.0887,-0.00203558,-0.163769
338,12:16:33.821 PM,0.0123568,2.0887,-0.00101962,-0.111734
339,12:16:34.021 PM,0.0123568,2.0887,-0.00203558,-0.111734
340,12:16:34.221 PM,0.0123568,2.0887,-0.00203558,-0.111734
341,12:16:34.421 PM,0.0123568,2.0887,-0.00101962,-0.111734
342,12:16:34.621 PM,0.0123568,2.0887,-0.00203558,-0.0857167
343,12:16:34.821 PM,0.0123568,2.0887,-0.00101962,-0.15076
344,12:16:35.021 PM,0.0123568,2.0887,-0.00203558,-0.15076
345,12:16:35.221 PM,0.0123568,2.0887,-0.00101962,-0.15076
346,12:16:35.421 PM,0.0133743,2.0887,-0.00203558,-0.176778
347,12:16:35.621 PM,0.0133743,2.0887,-0.00203558,-0.137751
348,12:16:35.821 PM,0.0133743,2.0887,-0.00101962,-0.15076
349,12:16:36.021 PM,0.0123568,2.0887,-0.00203558,-0.163769
350,12:16:36.221 PM,0.0113393,2.0887,-0.00101962,-0.163769
351,12:16:36.421 PM,0.0123568,2.0887,-0.00203558,-0.111734
352,12:16:36.621 PM,0.0123568,2.0887,-3.66674E-6,-0.15076
353,12:16:36.821 PM,0.0123568,2.0887,-0.00101962,-0.163769
354,12:16:37.021 PM,0.0123568,2.0887,-0.00203558,-0.137751
355,12:16:37.221 PM,0.0133743,2.0887,-0.00101962,-0.137751
356,12:16:37.421 PM,0.0133743,2.0887,-0.00101962,-0.163769
357,12:16:37.621 PM,0.0123568,2.0887,-0.00203558,-0.15076
358,12:16:37.821 PM,0.0133743,2.0887,-0.00203558,-0.15076
359,12:16:38.021 PM,0.0133743,2.0887,-0.00203558,-0.137751
360,12:16:38.221 PM,0.0133743,2.0887,-0.00101962,-0.176778
361,12:16:38.421 PM,0.0133743,2.0887,-0.00203558,-0.15076
362,12:16:38.621 PM,0.0123568,2.0887,-0.00101962,-0.124743
363,12:16:38.821 PM,0.0133743,2.0887,-0.00203558,-0.15076
364,12:16:39.021 PM,0.0133743,2.0887,-0.00203558,-0.124743
365,12:16:39.221 PM,0.0123568,2.0887,-0.00203558,-0.124743
366,12:16:39.421 PM,0.0123568,2.0887,-0.00203558,-0.163769
367,12:16:39.621 PM,0.0133743,2.0887,-0.00203558,-0.124743
368,12:16:39.821 PM,0.0133743,2.0887,-0.00203558,-0.137751
369,12:16:40.021 PM,0.0133743,2.0887,-0.00203558,-0.176778
370,12:16:40.221 PM,0.0133743,2.0887,-0.00203558,-0.163769
371,12:16:40.421 PM,0.0133743,2.0887,-0.00101962,-0.124743
372,12:16:40.621 PM,0.0143918,2.0887,-0.00101962,-0.163769
373,12:16:40.821 PM,0.0133743,2.0887,-0.00101962,-0.124743
374,12:16:41.021 PM,0.0133743,2.0887,-3.66674E-6,-0.111734
375,12:16:41.221 PM,0.0123568,2.0887,-0.00101962,-0.111734
376,12:16:41.421 PM,0.0133743,2.0887,-0.00203558,-0.189786
377,12:16:41.621 PM,0.0123568,2.0887,-0.00101962,-0.163769
378,12:16:41.821 PM,0.0133743,2.0887,-0.00101962,-0.189786
379,12:16:42.021 PM,0.0133743,2.0887,-0.00203558,-0.176778
380,12:16:42.221 PM,0.0133743,2.0887,-0.00203558,-0.111734
381,12:16:42.421 PM,0.0133743,2.0887,-0.00203558,-0.124743
382,12:16:42.621 PM,0.0133743,2.0887,-0.00101962,-0.15076
383,12:16:42.821 PM,0.0133743,2.0887,-0.00203558,-0.15076
384,12:16:43.021 PM,0.0133743,2.0887,-0.00203558,-0.137751
385,12:16:43.221 PM,0.0133743,2.0887,-0.00203558,-0.176778
386,12:16:43.421 PM,0.0123568,2.0887,-0.00203558,-0.176778
387,12:16:43.621 PM,0.0123568,2.0887,-0.00101962,-0.163769
388,12:16:43.821 PM,0.0133743,2.0887,-0.00101962,-0.111734
389,12:16:44.021 PM,0.0133743,2.0887,-0.00101962,-0.137751
390,12:16:44.221 PM,0.0133743,2.0887,-0.00203558,-0.124743
391,12:16:44.421 PM,0.0133743,2.0887,-0.00101962,-0.137751
392,12:16:44.621 PM,0.0133743,2.0887,-0.00203558,-0.176778
393,12:16:44.821 PM,0.0133743,2.0887,-0.00203558,-0.176778
394,12:16:45.021 PM,0.0133743,2.0887,-0.00203558,-0.15076
395,12:16:45.221 PM,0.0133743,2.0887,-0.00101962,-0.124743
396,12:16:45.421 PM,0.0133743,2.0887,-0.00101962,-0.163769
397,12:16:45.621 PM,0.0133743,2.0887,-0.00101962,-0.176778
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

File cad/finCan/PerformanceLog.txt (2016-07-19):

Mesh Preparation:  0 hr 0 min 0 sec
Standard solid mesh bolt head imprint and hard point processing:  0 hr 0 min 0 sec
Standard solid mesh total preparation including imprint:  0 hr 0 min 0 sec
Standard surface meshing for Solid Mesh:  0 hr 0 min 2 sec
Standard volume meshing for Solid Mesh:  0 hr 0 min 0 sec
Standard solid mesh arranging data:  0 hr 0 min 0 sec
Standard solid mesh total:  0 hr 0 min 2 sec
Beam mesh:  0 hr 0 min 0 sec
Mesh Preparation:  0 hr 0 min 0 sec
Standard solid mesh bolt head imprint and hard point processing:  0 hr 0 min 0 sec
Standard solid mesh total preparation including imprint:  0 hr 0 min 0 sec
Standard surface meshing for Solid Mesh:  0 hr 0 min 2 sec
Standard volume meshing for Solid Mesh:  0 hr 0 min 0 sec
Standard solid mesh arranging data:  0 hr 0 min 0 sec
Standard solid mesh total:  0 hr 0 min 2 sec
Beam mesh:  0 hr 0 min 0 sec
Mesh Preparation:  0 hr 0 min 0 sec
Standard solid mesh bolt head imprint and hard point processing:  0 hr 0 min 0 sec
Standard solid mesh total preparation including imprint:  0 hr 0 min 0 sec
Standard surface meshing for Solid Mesh:  0 hr 0 min 1 sec
Standard volume meshing for Solid Mesh:  0 hr 0 min 0 sec
Standard solid mesh arranging data:  0 hr 0 min 0 sec
Standard solid mesh total:  0 hr 0 min 1 sec
Beam mesh:  0 hr 0 min 0 sec
Mesh Preparation:  0 hr 0 min 0 sec
Standard solid mesh bolt head imprint and hard point processing:  0 hr 0 min 0 sec
Standard solid mesh total preparation including imprint:  0 hr 0 min 0 sec
Standard surface meshing for Solid Mesh:  0 hr 0 min 0 sec
Standard volume meshing for Solid Mesh:  0 hr 0 min 1 sec
Standard solid mesh arranging data:  0 hr 0 min 0 sec
Standard solid mesh total:  0 hr 0 min 2 sec
Beam mesh:  0 hr 0 min 0 sec
Mesh Preparation:  0 hr 0 min 0 sec
Standard solid mesh bolt head imprint and hard point processing:  0 hr 0 min 0 sec
Standard solid mesh total preparation including imprint:  0 hr 0 min 0 sec
Standard surface meshing for Solid Mesh:  0 hr 0 min 2 sec
Standard volume meshing for Solid Mesh:  0 hr 0 min 0 sec
Standard solid mesh arranging data:  0 hr 0 min 0 sec
Standard solid mesh total:  0 hr 0 min 2 sec
Beam mesh:  0 hr 0 min 0 sec
Mesh Preparation:  0 hr 0 min 0 sec
Standard solid mesh bolt head imprint and hard point processing:  0 hr 0 min 0 sec
Standard solid mesh total preparation including imprint:  0 hr 0 min 0 sec
Standard surface meshing for Solid Mesh:  0 hr 0 min 0 sec
Standard volume meshing for Solid Mesh:  0 hr 0 min 1 sec
Standard solid mesh arranging data:  0 hr 0 min 0 sec
Standard solid mesh total:  0 hr 0 min 2 sec
Beam mesh:  0 hr 0 min 0 sec
Mesh Preparation:  0 hr 0 min 0 sec
Standard solid mesh bolt head imprint and hard point processing:  0 hr 0 min 0 sec
Standard solid mesh total preparation including imprint:  0 hr 0 min 0 sec
Standard surface meshing for Solid Mesh:  0 hr 0 min 0 sec
Standard volume meshing for Solid Mesh:  0 hr 0 min 0 sec
Standard solid mesh total:  0 hr 1 min 33 sec
Beam mesh:  0 hr 0 min 0 sec
Mesh Preparation:  0 hr 0 min 0 sec
Standard solid mesh bolt head imprint and hard point processing:  0 hr 0 min 0 sec
Standard solid mesh total preparation including imprint:  0 hr 0 min 0 sec
Standard surface meshing for Solid Mesh:  0 hr 0 min 6 sec
Standard volume meshing for Solid Mesh:  0 hr 0 min 3 sec
Standard solid mesh arranging data:  0 hr 0 min 0 sec
Standard solid mesh total:  0 hr 0 min 9 sec
Beam mesh:  0 hr 0 min 0 sec
Preparing to transfer data:  0 hr 0 min 0 sec
Processing material properties:  0 hr 0 min 0 sec
Processing element groups:  0 hr 0 min 0 sec
Processing drop test gap nodes:  0 hr 0 min 0 sec
Updating thickness for shell regions:  0 hr 0 min 0 sec
Processing rconst for elements:  0 hr 0 min 0 sec
Processing egroups:  0 hr 0 min 0 sec
Transferring loads and boundary conditions:  0 hr 0 min 0 sec
Generating contacts:  0 hr 0 min 0 sec
Number of Contacts: 0
Transfer SL1 data:  0 hr 0 min 0 sec
Generate more accurate contact data:  0 hr 0 min 0 sec
Number of contact data: 0
Transfer beam/joint contact data:  0 hr 0 min 0 sec
Transferring other special loads:  0 hr 0 min 0 sec
Transferring bearing loads:  0 hr 0 min 0 sec
Transferring mass elements:  0 hr 0 min 0 sec
Transferring point loads:  0 hr 0 min 0 sec
Transferring distributed beam loads:  0 hr 0 min 0 sec
Transferring rigid bodies:  0 hr 0 min 0 sec
Transferring component no penetration:  0 hr 0 min 0 sec
Writing Data:  0 hr 0 min 0 sec
Transferring analysis options:  0 hr 0 min 1 sec
Total midsurf mapping:  0 hr 0 min 0 sec

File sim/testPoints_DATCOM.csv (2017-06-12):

 | X..Time..s. | Altitude..km. | Vertical.velocity..m.s. | Vertical.acceleration..m.s.. | Total.velocity..m.s. | Total.acceleration..m.s.. | Position.East.of.launch..km. | Position.North.of.launch..km. | Lateral.distance..km. | Lateral.direction.... | Lateral.velocity..m.s. | Lateral.acceleration..m.s.. | Latitude.... | Longitude.... | Gravitational.acceleration..m.s.. | Angle.of.attack.... | Roll.rate..r.s. | Pitch.rate..r.s. | Yaw.rate..r.s. | Mass..kg. | Propellant.mass..kg. | Longitudinal.moment.of.inertia..kg.m.. | Rotational.moment.of.inertia..kg.m.. | CP.location..in. | CG.location..in. | Stability.margin.calibers.... | Mach.number.... | Reynolds.number.... | Thrust..N. | Drag.force..N. | Drag.coefficient.... | Axial.drag.coefficient.... | Friction.drag.coefficient.... | Pressure.drag.coefficient.... | Base.drag.coefficient.... | Normal.force.coefficient.... | Pitch.moment.coefficient.... | Yaw.moment.coefficient.... | Side.force.coefficient.... | Roll.moment.coefficient.... | Roll.forcing.coefficient.... | Roll.damping.coefficient.... | Pitch.damping.coefficient.... | Coriolis.acceleration..m.s.. | Reference.length..in. | Reference.area..m.. |
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

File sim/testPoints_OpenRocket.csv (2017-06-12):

 | X..Time..s. | Altitude..km. | Vertical.velocity..m.s. | Vertical.acceleration..m.s.. | Total.velocity..m.s. | Total.acceleration..m.s.. | Position.East.of.launch..km. | Position.North.of.launch..km. | Lateral.distance..km. | Lateral.direction.... | Lateral.velocity..m.s. | Lateral.acceleration..m.s.. | Latitude.... | Longitude.... | Gravitational.acceleration..m.s.. | Angle.of.attack.... | Roll.rate..r.s. | Pitch.rate..r.s. | Yaw.rate..r.s. | Mass..kg. | Propellant.mass..kg. | Longitudinal.moment.of.inertia..kg.m.. | Rotational.moment.of.inertia..kg.m.. | CP.location..in. | CG.location..in. | Stability.margin.calibers.... | Mach.number.... | Reynolds.number.... | Thrust..N. | Drag.force..N. | Drag.coefficient.... | Axial.drag.coefficient.... | Friction.drag.coefficient.... | Pressure.drag.coefficient.... | Base.drag.coefficient.... | Normal.force.coefficient.... | Pitch.moment.coefficient.... | Yaw.moment.coefficient.... | Side.force.coefficient.... | Roll.moment.coefficient.... | Roll.forcing.coefficient.... | Roll.damping.coefficient.... | Pitch.damping.coefficient.... | Coriolis.acceleration..m.s.. | Reference.length..in. | Reference.area..m.. |
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

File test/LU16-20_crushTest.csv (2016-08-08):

NI VI Logger
Created: 9/29/2004 12:22:18.622 AM Pacific Daylight Time
Number of scans: 845
Scan rate: 0.2 seconds
Row | Time | Voltage_0(Voltage) | Voltage_1(Voltage) | Voltage_2(Voltage) | Voltage_3(Voltage)
1 | 12:16:48.234 AM | 0.000146639 | -0.207928 | 0.00459529 | -0.00330552
2 | 12:16:48.434 AM | -0.00188839 | -0.207928 | -0.000486211 | -0.00330552
3 | 12:16:48.634 AM | 0.000146639 | -0.207928 | -0.000486211 | -0.00330552
4 | 12:16:48.834 AM | -0.0029059 | -0.207928 | 0.00459529 | -0.00330552
5 | 12:16:49.034 AM | -0.00188839 | -0.207928 | -0.000486211 | -0.00330552
6 | 12:16:49.234 AM | -0.0029059 | -0.207928 | -0.000486211 | -0.00330552
7 | 12:16:49.434 AM | -0.00188839 | -0.207928 | -0.000486211 | -0.00330552
8 | 12:16:49.634 AM | -0.000870874 | -0.207928 | -0.000486211 | -0.00330552
9 | 12:16:49.834 AM | -0.00188839 | -0.207928 | -0.000486211 | -0.00330552
10 | 12:16:50.034 AM | -0.00188839 | -0.207928 | -0.000486211 | -0.00330552
11 | 12:16:50.234 AM | -0.00188839 | -0.207928 | -0.000486211 | -0.00330552
12 | 12:16:50.434 AM | -0.000870874 | -0.207928 | -0.000486211 | -0.00330552
13 | 12:16:50.634 AM | 0.000146639 | -0.207928 | -0.000486211 | -0.00330552
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

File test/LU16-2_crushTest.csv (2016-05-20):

NI VI Logger
Created: 5/12/2016 12:55:57.708 PM Pacific Daylight Time
Number of scans: 525
Scan rate: 0.2 seconds
Row | Time | Voltage_0(Voltage) | Voltage_1(Voltage) | Voltage_2(Voltage) | Voltage_3(Voltage)
1 | 12:53:11.765 PM | -0.00392341 | -0.00152882 | -3.66674E-6 | -0.371908
2 | 12:53:11.965 PM | -0.00392341 | -0.00152882 | -3.66674E-6 | -0.371908
3 | 12:53:12.165 PM | -0.00392341 | -0.0005122 | -3.66674E-6 | -0.410934
4 | 12:53:12.365 PM | -0.00494092 | -0.0005122 | -0.00101962 | -0.280847
5 | 12:53:12.565 PM | -0.00392341 | -0.0005122 | -3.66674E-6 | -0.358899
6 | 12:53:12.765 PM | -0.00392341 | -0.0005122 | -0.00101962 | -0.358899
7 | 12:53:12.965 PM | -0.00392341 | -0.00254544 | -3.66674E-6 | -0.384917
8 | 12:53:13.165 PM | -0.00494092 | -0.00152882 | -0.00101962 | -0.306865
9 | 12:53:13.365 PM | -0.0029059 | -0.0005122 | 0.00101229 | -0.397925
10 | 12:53:13.565 PM | -0.00392341 | -0.0005122 | -3.66674E-6 | -0.397925
11 | 12:53:13.765 PM | -0.00392341 | -0.00152882 | -0.00101962 | -0.25483
12 | 12:53:13.965 PM | -0.0029059 | -0.00254544 | -3.66674E-6 | -0.410934
13 | 12:53:14.165 PM | -0.00392341 | -0.00152882 | -3.66674E-6 | -0.306865
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

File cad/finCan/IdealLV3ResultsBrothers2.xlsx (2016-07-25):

 |  |  |  |  |  |  |  |  |  |  |  |  | Aspect Ratio: | 0.5583704211 |  | Shear Mod. Effective | 2380500000000000
 |  |  |  |  |  |  |  |  |  |  |  |  | Chord: | 0.2921 |  | Torsional Mod. | 6.330359694e-05
 |  |  |  |  |  |  |  |  |  |  |  |  | Taper Ratio: | 0.2778 |  | Shear Mod | 30000000000
 |  |  |  |  |  |  |  |  |  |  |  |  | Thickness | 0.00254
 |  |  |  |  |  |  |  |  |  |  |  |  | Span | 0.1631
Time (s) | Alt. (m) | Vertical Velocity (m/s) | Total Velocity (m/s) | Lat. Velocity (m/s) | CP location (cm) | CG location (cm) | Mach | Reynolds | Drag force (N) | Drag coeff | Axial Drag Coeff | Friction Drag Coeff | Pressure Drag Coeff | Base drag coeff | Temperature (°C) | Pressure (mbar) | Speed of Sound (m/s) | Flutter Velocity, Aluminum (m/s) | Velocity Buffer (m/s)
0.02 | 0.00087735 | 0.17548 | 0.17548 | 0 | NaN | 217.21 | 0.014947 | 963387 | 1.5549e-05 | 0.49 | 5.248e-05 | 0.36625 | 0.0084245 | 0.12003 | 6.03 | 858.32 | 334.95 | 34830.82573 | 34830.65025
0.03 | 0.0044216 | 0.53338 | 0.53338 | 0 | NaN | 217.2 | 0.014898 | 960232 | 0.00042148 | 0.49 | 0.0014319 | 0.36649 | 0.0084245 | 0.12003 | 6.03 | 858.32 | 334.95 | 34830.82573 | 34830.29235
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

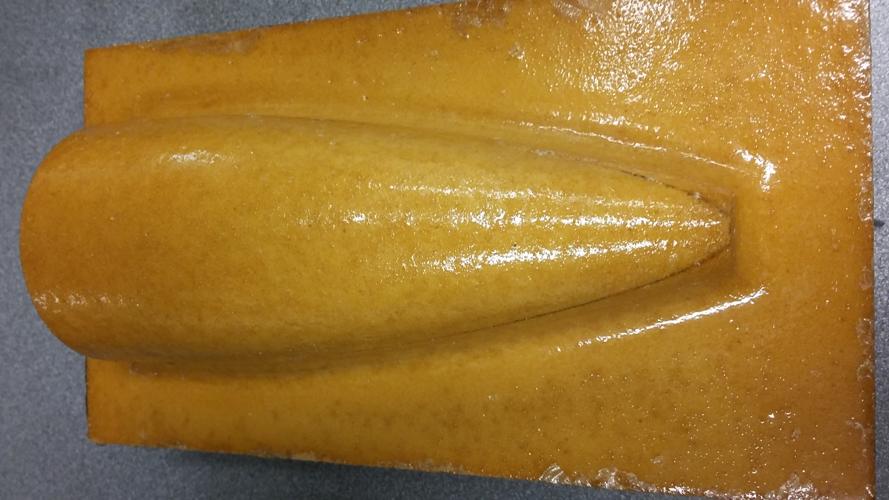
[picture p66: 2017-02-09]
doc/img/tinyTestMold_afterEpoxy.jpg

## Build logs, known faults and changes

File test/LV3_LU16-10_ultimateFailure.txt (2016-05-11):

NI VI Logger                            
Created: 4/29/2016 11:43:40.075 AM Pacific Daylight Time
Number of scans: 3780
Scan rate: 0.2 seconds

Row,Time,Voltage_0(Voltage),Voltage_1(Voltage),Voltage_2(Voltage),Voltage_3(Voltage)
1,11:30:50.078 AM,0.000146639,-0.0005122,-3.66674E-6,-0.137751
2,11:30:50.278 AM,-0.000870874,0.000504419,-3.66674E-6,-0.111734
3,11:30:50.478 AM,0.000146639,0.000504419,-0.00203558,-0.0987254
4,11:30:50.678 AM,-0.000870874,0.000504419,0.00101229,-0.111734
5,11:30:50.878 AM,-0.000870874,0.00152104,-3.66674E-6,-0.124743
6,11:30:51.078 AM,0.000146639,0.000504419,-0.00101962,-0.072708
7,11:30:51.278 AM,-0.000870874,0.00152104,-3.66674E-6,-0.15076
8,11:30:51.478 AM,-0.00188839,0.000504419,-0.00101962,-0.111734
9,11:30:51.678 AM,-0.000870874,0.000504419,-3.66674E-6,-0.0987254
10,11:30:51.878 AM,-0.00188839,0.000504419,-3.66674E-6,-0.124743
11,11:30:52.078 AM,0.000146639,0.000504419,-0.00101962,-0.137751
12,11:30:52.278 AM,-0.000870874,0.000504419,-3.66674E-6,-0.111734
13,11:30:52.478 AM,-0.000870874,-0.0005122,-0.00101962,-0.124743
14,11:30:52.678 AM,-0.000870874,0.000504419,-0.00101962,-0.072708
15,11:30:52.878 AM,-0.000870874,0.000504419,-3.66674E-6,-0.0987254
16,11:30:53.078 AM,-0.000870874,0.000504419,-3.66674E-6,-0.137751
17,11:30:53.278 AM,-0.000870874,-0.0005122,-3.66674E-6,-0.111734
18,11:30:53.478 AM,-0.000870874,0.00152104,-0.00101962,-0.111734
19,11:30:53.678 AM,-0.000870874,0.000504419,-0.00101962,-0.124743
20,11:30:53.878 AM,-0.000870874,-0.0005122,-0.00101962,-0.111734
21,11:30:54.078 AM,-0.000870874,0.00152104,-3.66674E-6,-0.137751
22,11:30:54.278 AM,-0.000870874,-0.0005122,-0.00101962,-0.111734
23,11:30:54.478 AM,-0.000870874,0.000504419,-0.00203558,-0.111734
24,11:30:54.678 AM,-0.000870874,0.000504419,-3.66674E-6,-0.0857167
25,11:30:54.878 AM,-0.000870874,-0.0005122,-3.66674E-6,-0.0857167
26,11:30:55.078 AM,-0.000870874,0.000504419,-0.00101962,-0.111734
27,11:30:55.278 AM,-0.000870874,0.00152104,-3.66674E-6,-0.111734
28,11:30:55.478 AM,-0.000870874,0.000504419,-3.66674E-6,-0.111734
29,11:30:55.678 AM,-0.000870874,-0.0005122,-3.66674E-6,-0.124743
30,11:30:55.878 AM,0.000146639,0.000504419,-3.66674E-6,-0.124743
31,11:30:56.078 AM,0.000146639,-0.0005122,-3.66674E-6,-0.111734
32,11:30:56.278 AM,-0.000870874,-0.0005122,-0.00101962,-0.124743
33,11:30:56.478 AM,-0.000870874,0.000504419,-3.66674E-6,-0.111734
34,11:30:56.678 AM,-0.000870874,-0.0005122,-3.66674E-6,-0.15076
35,11:30:56.878 AM,-0.000870874,-0.0005122,-0.00101962,-0.124743
36,11:30:57.078 AM,0.000146639,0.000504419,-3.66674E-6,-0.124743
37,11:30:57.278 AM,-0.000870874,-0.0005122,-0.00101962,-0.176778
38,11:30:57.478 AM,-0.000870874,0.000504419,-0.00101962,-0.15076
39,11:30:57.678 AM,0.000146639,0.000504419,-3.66674E-6,-0.137751
40,11:30:57.878 AM,-0.000870874,-0.0005122,-3.66674E-6,-0.124743
41,11:30:58.078 AM,-0.000870874,0.000504419,-0.00101962,-0.163769
42,11:30:58.278 AM,-0.000870874,0.000504419,-0.00101962,-0.124743
43,11:30:58.478 AM,-0.000870874,0.000504419,-3.66674E-6,-0.15076
44,11:30:58.678 AM,0.000146639,0.000504419,-0.00101962,-0.111734
45,11:30:58.878 AM,-0.000870874,0.000504419,-0.00101962,-0.111734
46,11:30:59.078 AM,-0.000870874,0.000504419,-3.66674E-6,-0.0987254
47,11:30:59.278 AM,-0.00188839,0.000504419,-0.00101962,-0.111734
48,11:30:59.478 AM,-0.000870874,0.000504419,-0.00101962,-0.111734
49,11:30:59.678 AM,-0.000870874,0.00152104,-0.00101962,-0.111734
50,11:30:59.878 AM,-0.000870874,0.000504419,-0.00101962,-0.124743
51,11:31:00.078 AM,-0.000870874,0.000504419,-0.00101962,-0.0987254
52,11:31:00.278 AM,-0.000870874,0.000504419,-3.66674E-6,-0.15076
53,11:31:00.478 AM,-0.000870874,0.000504419,-3.66674E-6,-0.0987254
54,11:31:00.678 AM,-0.000870874,0.000504419,-0.00101962,-0.124743
55,11:31:00.878 AM,-0.000870874,0.000504419,-3.66674E-6,-0.124743
56,11:31:01.078 AM,-0.000870874,0.000504419,-0.00101962,-0.111734
57,11:31:01.278 AM,-0.000870874,0.00152104,-0.00101962,-0.111734
58,11:31:01.478 AM,-0.000870874,0.000504419,-3.66674E-6,-0.0987254
59,11:31:01.678 AM,-0.000870874,0.000504419,-0.00101962,-0.0987254
60,11:31:01.878 AM,-0.000870874,0.00152104,-3.66674E-6,-0.111734
61,11:31:02.078 AM,-0.000870874,0.000504419,-0.00101962,-0.0857167
62,11:31:02.278 AM,-0.000870874,0.000504419,0.00101229,-0.0857167
63,11:31:02.478 AM,-0.000870874,0.000504419,-0.00101962,-0.0987254
64,11:31:02.678 AM,-0.000870874,0.000504419,-0.00101962,-0.111734
65,11:31:02.878 AM,-0.000870874,0.000504419,-0.00101962,-0.15076
66,11:31:03.078 AM,-0.000870874,0.000504419,-0.00101962,-0.124743
67,11:31:03.278 AM,-0.000870874,0.000504419,-3.66674E-6,-0.124743
68,11:31:03.478 AM,-0.000870874,0.000504419,-3.66674E-6,-0.124743
69,11:31:03.678 AM,-0.000870874,-0.0005122,-3.66674E-6,-0.124743
70,11:31:03.878 AM,-0.000870874,-0.0005122,-0.00101962,-0.124743
71,11:31:04.078 AM,-0.000870874,0.000504419,-0.00101962,-0.15076
72,11:31:04.278 AM,-0.00188839,0.000504419,-0.00101962,-0.111734
73,11:31:04.478 AM,-0.000870874,0.00152104,-0.00101962,-0.137751
74,11:31:04.678 AM,-0.000870874,0.000504419,-3.66674E-6,-0.215804
75,11:31:04.878 AM,-0.000870874,0.000504419,-0.00203558,-0.15076
76,11:31:05.078 AM,-0.000870874,0.000504419,-3.66674E-6,-0.15076
77,11:31:05.278 AM,-0.000870874,0.000504419,-3.66674E-6,-0.15076
78,11:31:05.478 AM,0.000146639,0.000504419,-0.00101962,-0.163769
79,11:31:05.678 AM,0.000146639,0.000504419,-0.00101962,-0.137751
80,11:31:05.878 AM,-0.00188839,-0.0005122,-0.00101962,-0.0987254
81,11:31:06.078 AM,-0.000870874,-0.0005122,-0.00101962,-0.0987254
82,11:31:06.278 AM,-0.000870874,0.000504419,-0.00101962,-0.0987254
83,11:31:06.478 AM,-0.00188839,0.000504419,-3.66674E-6,-0.137751
84,11:31:06.678 AM,-0.000870874,0.000504419,-0.00101962,-0.111734
85,11:31:06.878 AM,-0.000870874,0.000504419,-3.66674E-6,-0.137751
86,11:31:07.078 AM,0.000146639,0.000504419,0.00101229,-0.15076
87,11:31:07.278 AM,0.000146639,-0.0005122,-3.66674E-6,-0.0987254
88,11:31:07.478 AM,-0.000870874,0.00152104,-3.66674E-6,-0.176778
89,11:31:07.678 AM,-0.000870874,0.000504419,-0.00101962,-0.124743
90,11:31:07.878 AM,-0.000870874,0.000504419,-3.66674E-6,-0.124743
91,11:31:08.078 AM,-0.000870874,0.000504419,-3.66674E-6,-0.137751
92,11:31:08.278 AM,-0.000870874,0.000504419,-0.00101962,-0.176778
93,11:31:08.478 AM,-0.000870874,0.00152104,-3.66674E-6,-0.124743
94,11:31:08.678 AM,-0.000870874,0.000504419,-3.66674E-6,-0.163769
95,11:31:08.878 AM,0.000146639,-0.0005122,-0.00101962,-0.189786
96,11:31:09.078 AM,-0.000870874,-0.0005122,-0.00101962,-0.176778
97,11:31:09.278 AM,-0.000870874,0.000504419,-0.00101962,-0.124743
98,11:31:09.478 AM,-0.000870874,-0.0005122,-3.66674E-6,-0.176778
99,11:31:09.678 AM,-0.000870874,0.00152104,-0.00101962,-0.215804
100,11:31:09.878 AM,-0.000870874,0.000504419,-3.66674E-6,-0.137751
101,11:31:10.078 AM,-0.000870874,-0.0005122,-3.66674E-6,-0.176778
102,11:31:10.278 AM,-0.000870874,0.00152104,-3.66674E-6,-0.15076
103,11:31:10.478 AM,-0.000870874,0.000504419,-0.00101962,-0.163769
104,11:31:10.678 AM,-0.000870874,0.000504419,-0.00101962,-0.176778
105,11:31:10.878 AM,-0.000870874,0.000504419,-0.00101962,-0.176778
106,11:31:11.078 AM,-0.000870874,0.000504419,-3.66674E-6,-0.124743
107,11:31:11.278 AM,-0.000870874,0.000504419,-0.00101962,-0.137751
108,11:31:11.478 AM,-0.00188839,-0.0005122,-0.00101962,-0.124743
109,11:31:11.678 AM,-0.00188839,0.000504419,-3.66674E-6,-0.137751
110,11:31:11.878 AM,-0.000870874,0.000504419,-0.00101962,-0.15076
111,11:31:12.078 AM,-0.000870874,0.00152104,-0.00101962,-0.176778
112,11:31:12.278 AM,-0.000870874,0.000504419,-3.66674E-6,-0.163769
113,11:31:12.478 AM,-0.000870874,0.000504419,-0.00101962,-0.176778
114,11:31:12.678 AM,0.000146639,-0.0005122,-0.00101962,-0.137751
115,11:31:12.878 AM,-0.000870874,0.000504419,-3.66674E-6,-0.163769
116,11:31:13.078 AM,-0.00188839,0.000504419,-0.00101962,-0.189786
117,11:31:13.278 AM,-0.000870874,0.000504419,-0.00101962,-0.176778
118,11:31:13.478 AM,-0.000870874,0.000504419,-0.00101962,-0.241821
119,11:31:13.678 AM,-0.00188839,0.000504419,-0.00101962,-0.241821
120,11:31:13.878 AM,-0.000870874,0.000504419,-0.00101962,-0.241821
121,11:31:14.078 AM,-0.000870874,0.000504419,-3.66674E-6,-0.202795
122,11:31:14.278 AM,-0.00188839,0.00152104,-0.00101962,-0.15076
123,11:31:14.478 AM,-0.000870874,0.000504419,-3.66674E-6,-0.202795
124,11:31:14.678 AM,-0.00188839,0.000504419,-3.66674E-6,-0.176778
125,11:31:14.878 AM,-0.00188839,0.000504419,-0.00101962,-0.215804
126,11:31:15.078 AM,-0.000870874,-0.0005122,-0.00101962,-0.176778
127,11:31:15.278 AM,-0.000870874,0.000504419,-0.00101962,-0.15076
128,11:31:15.478 AM,-0.000870874,0.000504419,-3.66674E-6,-0.241821
129,11:31:15.678 AM,-0.000870874,0.00152104,-0.00101962,-0.163769
130,11:31:15.878 AM,-0.000870874,0.000504419,-0.00101962,-0.176778
131,11:31:16.078 AM,-0.000870874,0.000504419,-3.66674E-6,-0.189786
132,11:31:16.278 AM,-0.00188839,0.000504419,-3.66674E-6,-0.241821
133,11:31:16.478 AM,0.000146639,0.000504419,-0.00101962,-0.202795
134,11:31:16.678 AM,-0.000870874,0.000504419,-0.00101962,-0.189786
135,11:31:16.878 AM,-0.000870874,0.000504419,-0.00101962,-0.189786
136,11:31:17.078 AM,-0.000870874,0.000504419,-0.00101962,-0.176778
137,11:31:17.278 AM,-0.000870874,-0.0005122,-0.00101962,-0.163769
138,11:31:17.478 AM,-0.000870874,-0.0005122,-3.66674E-6,-0.176778
139,11:31:17.678 AM,-0.000870874,0.000504419,-0.00101962,-0.202795
140,11:31:17.878 AM,-0.000870874,0.00152104,-0.00101962,-0.202795
141,11:31:18.078 AM,-0.000870874,0.000504419,-0.00101962,-0.202795
142,11:31:18.278 AM,-0.00188839,-0.0005122,-0.00101962,-0.189786
143,11:31:18.478 AM,-0.000870874,0.000504419,-3.66674E-6,-0.215804
144,11:31:18.678 AM,-0.000870874,-0.0005122,-3.66674E-6,-0.163769
145,11:31:18.878 AM,0.000146639,0.000504419,-0.00101962,-0.202795
146,11:31:19.078 AM,0.000146639,0.000504419,-0.00101962,-0.189786
147,11:31:19.278 AM,-0.000870874,-0.0005122,-0.00101962,-0.215804
148,11:31:19.478 AM,-0.000870874,0.000504419,-3.66674E-6,-0.202795
149,11:31:19.678 AM,-0.000870874,0.000504419,-0.00101962,-0.176778
150,11:31:19.878 AM,-0.00188839,-0.0005122,-0.00101962,-0.163769
151,11:31:20.078 AM,-0.000870874,0.000504419,-0.00101962,-0.228812
152,11:31:20.278 AM,-0.000870874,0.000504419,-0.00101962,-0.189786
153,11:31:20.478 AM,-0.000870874,0.000504419,-3.66674E-6,-0.215804
154,11:31:20.678 AM,-0.000870874,-0.0005122,-0.00101962,-0.176778
155,11:31:20.878 AM,-0.000870874,0.000504419,-0.00101962,-0.215804
156,11:31:21.078 AM,0.000146639,0.000504419,0.00101229,-0.241821
157,11:31:21.278 AM,-0.000870874,0.00152104,-3.66674E-6,-0.280847
158,11:31:21.478 AM,-0.000870874,-0.0005122,-0.00101962,-0.241821
159,11:31:21.678 AM,-0.000870874,0.000504419,-0.00101962,-0.228812
160,11:31:21.878 AM,-0.00188839,0.00152104,-0.00101962,-0.280847
161,11:31:22.078 AM,-0.000870874,-0.0005122,-0.00101962,-0.215804
162,11:31:22.278 AM,0.000146639,0.000504419,-0.00101962,-0.228812
163,11:31:22.478 AM,0.000146639,-0.0005122,-3.66674E-6,-0.228812
164,11:31:22.678 AM,-0.000870874,0.000504419,-0.00101962,-0.228812
165,11:31:22.878 AM,-0.00188839,0.000504419,-0.00101962,-0.189786
166,11:31:23.078 AM,-0.000870874,0.000504419,-0.00101962,-0.202795
167,11:31:23.278 AM,0.000146639,0.000504419,-0.00101962,-0.241821
168,11:31:23.478 AM,-0.000870874,0.000504419,-0.00101962,-0.228812
169,11:31:23.678 AM,-0.000870874,0.000504419,-0.00101962,-0.25483
170,11:31:23.878 AM,-0.000870874,0.000504419,-0.00101962,-0.202795
171,11:31:24.078 AM,-0.000870874,0.000504419,-3.66674E-6,-0.202795
172,11:31:24.278 AM,-0.000870874,0.000504419,-3.66674E-6,-0.280847
173,11:31:24.478 AM,-0.00188839,-0.0005122,-0.00101962,-0.215804
174,11:31:24.678 AM,-0.000870874,-0.0005122,-0.00101962,-0.202795
175,11:31:24.878 AM,-0.00188839,0.00152104,-0.00101962,-0.215804
176,11:31:25.078 AM,-0.000870874,0.000504419,-0.00101962,-0.202795
177,11:31:25.278 AM,-0.000870874,0.000504419,-3.66674E-6,-0.202795
178,11:31:25.478 AM,-0.00188839,-0.0005122,-3.66674E-6,-0.241821
179,11:31:25.678 AM,-0.000870874,-0.0005122,-3.66674E-6,-0.189786
180,11:31:25.878 AM,0.000146639,0.000504419,-0.00101962,-0.25483
181,11:31:26.078 AM,-0.000870874,0.00152104,-3.66674E-6,-0.241821
182,11:31:26.278 AM,-0.000870874,0.000504419,-3.66674E-6,-0.215804
183,11:31:26.478 AM,-0.000870874,0.000504419,-0.00101962,-0.280847
184,11:31:26.678 AM,-0.000870874,0.000504419,-0.00101962,-0.241821
185,11:31:26.878 AM,-0.000870874,0.000504419,-3.66674E-6,-0.332882
186,11:31:27.078 AM,-0.000870874,-0.0005122,-0.00101962,-0.25483
187,11:31:27.278 AM,-0.000870874,0.000504419,-0.00101962,-0.293856
188,11:31:27.478 AM,-0.000870874,0.000504419,-3.66674E-6,-0.215804
189,11:31:27.678 AM,-0.000870874,0.00152104,-0.00203558,-0.267838
190,11:31:27.878 AM,-0.000870874,-0.0005122,-0.00101962,-0.215804
191,11:31:28.078 AM,0.000146639,0.000504419,-0.00203558,-0.25483
192,11:31:28.278 AM,-0.000870874,0.000504419,-0.00101962,-0.280847
193,11:31:28.478 AM,0.000146639,0.000504419,-3.66674E-6,-0.228812
194,11:31:28.678 AM,-0.000870874,-0.0005122,-0.00101962,-0.25483
195,11:31:28.878 AM,-0.000870874,0.000504419,-3.66674E-6,-0.241821
196,11:31:29.078 AM,0.000146639,0.000504419,-0.00101962,-0.280847
197,11:31:29.278 AM,-0.000870874,0.00152104,-0.00101962,-0.215804
198,11:31:29.478 AM,-0.000870874,-0.0005122,-0.00101962,-0.228812
199,11:31:29.678 AM,-0.000870874,0.000504419,-0.00101962,-0.293856
200,11:31:29.878 AM,-0.000870874,0.000504419,-3.66674E-6,-0.267838
201,11:31:30.078 AM,-0.000870874,-0.0005122,-0.00101962,-0.280847
202,11:31:30.278 AM,-0.000870874,0.000504419,-0.00101962,-0.293856
203,11:31:30.478 AM,-0.000870874,0.000504419,-3.66674E-6,-0.280847
204,11:31:30.678 AM,-0.000870874,0.000504419,-3.66674E-6,-0.332882
205,11:31:30.878 AM,-0.000870874,-0.0005122,-0.00101962,-0.293856
206,11:31:31.078 AM,-0.000870874,0.000504419,-3.66674E-6,-0.25483
207,11:31:31.278 AM,-0.000870874,0.000504419,-3.66674E-6,-0.241821
208,11:31:31.478 AM,0.000146639,0.000504419,-0.00101962,-0.228812
209,11:31:31.678 AM,-0.000870874,-0.0005122,-3.66674E-6,-0.241821
210,11:31:31.878 AM,-0.000870874,0.000504419,-0.00101962,-0.293856
211,11:31:32.078 AM,0.000146639,0.00152104,-3.66674E-6,-0.228812
212,11:31:32.278 AM,-0.000870874,-0.0005122,-0.00101962,-0.280847
213,11:31:32.478 AM,-0.00188839,-0.0005122,-0.00101962,-0.228812
214,11:31:32.678 AM,-0.000870874,-0.0005122,-3.66674E-6,-0.280847
215,11:31:32.878 AM,-0.000870874,0.00152104,-3.66674E-6,-0.306865
216,11:31:33.078 AM,-0.000870874,0.000504419,-0.00101962,-0.306865
217,11:31:33.278 AM,-0.000870874,-0.0005122,-0.00101962,-0.293856
218,11:31:33.478 AM,0.000146639,-0.0005122,-0.00203558,-0.358899
219,11:31:33.678 AM,-0.000870874,0.000504419,-3.66674E-6,-0.332882
220,11:31:33.878 AM,0.000146639,0.000504419,-0.00101962,-0.423943
221,11:31:34.078 AM,0.000146639,0.000504419,-0.00101962,-0.306865
222,11:31:34.278 AM,-0.000870874,0.000504419,-3.66674E-6,-0.332882
223,11:31:34.478 AM,-0.000870874,0.000504419,-0.00101962,-0.280847
224,11:31:34.678 AM,-0.000870874,0.000504419,-3.66674E-6,-0.280847
225,11:31:34.878 AM,0.000146639,0.000504419,-3.66674E-6,-0.267838
226,11:31:35.078 AM,-0.000870874,0.000504419,-0.00101962,-0.25483
227,11:31:35.278 AM,-0.000870874,-0.0005122,-0.00101962,-0.306865
228,11:31:35.478 AM,-0.000870874,0.000504419,-3.66674E-6,-0.293856
229,11:31:35.678 AM,-0.000870874,-0.0005122,-3.66674E-6,-0.241821
230,11:31:35.878 AM,-0.000870874,0.00152104,-0.00101962,-0.280847
231,11:31:36.078 AM,-0.000870874,0.000504419,-0.00101962,-0.280847
232,11:31:36.278 AM,-0.000870874,0.000504419,-3.66674E-6,-0.293856
233,11:31:36.478 AM,-0.00188839,0.000504419,-3.66674E-6,-0.228812
234,11:31:36.678 AM,-0.000870874,0.000504419,-0.00101962,-0.25483
235,11:31:36.878 AM,-0.00188839,-0.0005122,-3.66674E-6,-0.241821
236,11:31:37.078 AM,-0.000870874,0.000504419,-3.66674E-6,-0.293856
237,11:31:37.278 AM,0.000146639,-0.0005122,-0.00101962,-0.306865
238,11:31:37.478 AM,-0.00188839,-0.0005122,-3.66674E-6,-0.358899
239,11:31:37.678 AM,-0.000870874,0.000504419,-3.66674E-6,-0.306865
240,11:31:37.878 AM,0.000146639,-0.0005122,-3.66674E-6,-0.319873
241,11:31:38.078 AM,-0.000870874,-0.0005122,-3.66674E-6,-0.319873
242,11:31:38.278 AM,0.000146639,0.000504419,-3.66674E-6,-0.25483
243,11:31:38.478 AM,-0.00188839,-0.0005122,-0.00203558,-0.267838
244,11:31:38.678 AM,-0.000870874,-0.0005122,-3.66674E-6,-0.293856
245,11:31:38.878 AM,-0.000870874,0.000504419,-0.00101962,-0.228812
246,11:31:39.078 AM,-0.000870874,-0.0005122,-3.66674E-6,-0.228812
247,11:31:39.278 AM,-0.000870874,-0.0005122,-0.00101962,-0.228812
248,11:31:39.478 AM,-0.000870874,0.000504419,-0.00203558,-0.241821
249,11:31:39.678 AM,0.000146639,0.00152104,-0.00101962,-0.202795
250,11:31:39.878 AM,-0.000870874,0.000504419,-3.66674E-6,-0.215804
251,11:31:40.078 AM,-0.000870874,0.000504419,-0.00101962,-0.293856
252,11:31:40.278 AM,0.000146639,0.000504419,-0.00101962,-0.293856
253,11:31:40.478 AM,-0.000870874,0.000504419,-3.66674E-6,-0.293856
254,11:31:40.678 AM,-0.000870874,0.000504419,-0.00101962,-0.280847
255,11:31:40.878 AM,-0.000870874,0.000504419,-0.00101962,-0.267838
256,11:31:41.078 AM,-0.000870874,0.000504419,-0.00101962,-0.25483
257,11:31:41.278 AM,-0.000870874,0.000504419,0.00101229,-0.241821
258,11:31:41.478 AM,-0.000870874,-0.0005122,-0.00101962,-0.25483
259,11:31:41.678 AM,-0.000870874,-0.0005122,-0.00101962,-0.293856
260,11:31:41.878 AM,0.000146639,0.000504419,-0.00101962,-0.25483
261,11:31:42.078 AM,-0.000870874,0.000504419,-3.66674E-6,-0.228812
262,11:31:42.278 AM,-0.000870874,0.000504419,-3.66674E-6,-0.267838
263,11:31:42.478 AM,-0.000870874,0.000504419,-3.66674E-6,-0.25483
264,11:31:42.678 AM,-0.000870874,0.000504419,-3.66674E-6,-0.293856
265,11:31:42.878 AM,-0.000870874,0.000504419,-0.00101962,-0.25483
266,11:31:43.078 AM,-0.000870874,0.000504419,-0.00101962,-0.267838
267,11:31:43.278 AM,-0.000870874,0.000504419,-0.00101962,-0.280847
268,11:31:43.478 AM,-0.000870874,-0.0005122,-0.00101962,-0.241821
269,11:31:43.678 AM,-0.000870874,0.000504419,-0.00101962,-0.280847
270,11:31:43.878 AM,-0.000870874,-0.0005122,-0.00101962,-0.280847
271,11:31:44.078 AM,0.000146639,0.000504419,-0.00101962,-0.293856
272,11:31:44.278 AM,-0.000870874,0.000504419,-3.66674E-6,-0.280847
273,11:31:44.478 AM,0.000146639,0.00152104,-0.00101962,-0.241821
274,11:31:44.678 AM,-0.000870874,-0.0005122,-0.00101962,-0.241821
275,11:31:44.878 AM,-0.000870874,0.000504419,-0.00101962,-0.306865
276,11:31:45.078 AM,-0.000870874,-0.0005122,-3.66674E-6,-0.280847
277,11:31:45.278 AM,-0.000870874,-0.0005122,-0.00101962,-0.306865
278,11:31:45.478 AM,-0.000870874,-0.0005122,-0.00101962,-0.293856
279,11:31:45.678 AM,-0.000870874,0.000504419,-3.66674E-6,-0.280847
280,11:31:45.878 AM,-0.000870874,0.000504419,-3.66674E-6,-0.25483
281,11:31:46.078 AM,-0.000870874,0.000504419,-0.00101962,-0.25483
282,11:31:46.278 AM,-0.000870874,0.000504419,-0.00101962,-0.306865
283,11:31:46.478 AM,-0.000870874,0.000504419,-3.66674E-6,-0.241821
284,11:31:46.678 AM,-0.00188839,0.000504419,-3.66674E-6,-0.319873
285,11:31:46.878 AM,-0.000870874,0.000504419,-0.00203558,-0.25483
286,11:31:47.078 AM,-0.00188839,0.000504419,-3.66674E-6,-0.280847
287,11:31:47.278 AM,0.000146639,0.000504419,-0.00101962,-0.215804
288,11:31:47.478 AM,-0.000870874,-0.0005122,-3.66674E-6,-0.202795
289,11:31:47.678 AM,-0.000870874,0.00152104,-0.00101962,-0.25483
290,11:31:47.878 AM,-0.00188839,0.00152104,-0.00101962,-0.280847
291,11:31:48.078 AM,-0.000870874,0.000504419,-0.00101962,-0.280847
292,11:31:48.278 AM,-0.000870874,-0.0005122,-0.00101962,-0.267838
293,11:31:48.478 AM,-0.000870874,0.000504419,-3.66674E-6,-0.280847
294,11:31:48.678 AM,-0.000870874,-0.0005122,-0.00101962,-0.280847
295,11:31:48.878 AM,-0.000870874,0.000504419,-0.00101962,-0.293856
296,11:31:49.078 AM,-0.000870874,0.000504419,-0.00101962,-0.241821
297,11:31:49.278 AM,-0.000870874,0.000504419,-0.00203558,-0.280847
298,11:31:49.478 AM,0.000146639,-0.0005122,-0.00101962,-0.267838
299,11:31:49.678 AM,-0.000870874,0.00152104,-0.00101962,-0.228812
300,11:31:49.878 AM,-0.000870874,0.000504419,-3.66674E-6,-0.319873
301,11:31:50.078 AM,-0.000870874,-0.0005122,-0.00101962,-0.267838
302,11:31:50.278 AM,-0.000870874,0.000504419,-0.00101962,-0.280847
303,11:31:50.478 AM,-0.000870874,-0.0005122,-3.66674E-6,-0.280847
304,11:31:50.678 AM,-0.000870874,0.000504419,-0.00101962,-0.267838
305,11:31:50.878 AM,-0.00188839,0.000504419,-3.66674E-6,-0.280847
306,11:31:51.078 AM,-0.000870874,0.000504419,-0.00101962,-0.25483
307,11:31:51.278 AM,-0.000870874,0.000504419,-0.00101962,-0.25483
308,11:31:51.478 AM,-0.000870874,0.000504419,-0.00101962,-0.267838
309,11:31:51.678 AM,0.000146639,0.000504419,-3.66674E-6,-0.280847
310,11:31:51.878 AM,-0.000870874,-0.0005122,-0.00101962,-0.267838
311,11:31:52.078 AM,-0.000870874,-0.0005122,-0.00203558,-0.228812
312,11:31:52.278 AM,-0.00188839,0.000504419,-3.66674E-6,-0.267838
313,11:31:52.478 AM,-0.000870874,0.000504419,-0.00101962,-0.215804
314,11:31:52.678 AM,-0.00188839,0.00152104,-3.66674E-6,-0.189786
315,11:31:52.878 AM,-0.000870874,0.000504419,-3.66674E-6,-0.25483
316,11:31:53.078 AM,-0.000870874,0.000504419,-0.00101962,-0.215804
317,11:31:53.278 AM,-0.000870874,-0.0005122,-3.66674E-6,-0.189786
318,11:31:53.478 AM,-0.0029059,-0.0005122,-0.00101962,-0.189786
319,11:31:53.678 AM,-0.00392341,-0.0005122,-0.00101962,-0.137751
320,11:31:53.878 AM,-0.0029059,-0.0005122,-0.00101962,-0.176778
321,11:31:54.078 AM,-0.00392341,-0.0005122,-3.66674E-6,-0.176778
322,11:31:54.278 AM,-0.00392341,-0.00152882,-0.00101962,-0.15076
323,11:31:54.478 AM,-0.00392341,-0.0005122,-0.00101962,-0.163769
324,11:31:54.678 AM,-0.0029059,-0.0005122,-0.00101962,-0.176778
325,11:31:54.878 AM,-0.00494092,-0.00152882,-0.00101962,-0.15076
326,11:31:55.078 AM,-0.00392341,-0.00152882,-0.00101962,-0.163769
327,11:31:55.278 AM,-0.00494092,-0.00152882,-0.00101962,-0.163769
328,11:31:55.478 AM,-0.00494092,-0.0005122,-0.00101962,-0.137751
329,11:31:55.678 AM,-0.00494092,-0.00152882,-3.66674E-6,-0.111734
330,11:31:55.878 AM,-0.00494092,-0.00152882,-0.00101962,-0.15076
331,11:31:56.078 AM,-0.00494092,-0.00152882,-0.00203558,-0.163769
332,11:31:56.278 AM,-0.00494092,-0.00152882,-3.66674E-6,-0.176778
333,11:31:56.478 AM,-0.00494092,-0.00152882,-3.66674E-6,-0.202795
334,11:31:56.678 AM,-0.00392341,-0.00152882,-0.00101962,-0.176778
335,11:31:56.878 AM,-0.00392341,-0.00152882,-3.66674E-6,-0.15076
336,11:31:57.078 AM,-0.00392341,-0.00152882,-0.00101962,-0.176778
337,11:31:57.278 AM,-0.00494092,-0.00152882,-3.66674E-6,-0.228812
338,11:31:57.478 AM,-0.00494092,-0.00152882,-3.66674E-6,-0.189786
339,11:31:57.678 AM,-0.00392341,-0.0005122,-0.00101962,-0.202795
340,11:31:57.878 AM,-0.00494092,-0.0005122,-3.66674E-6,-0.241821
341,11:31:58.078 AM,-0.00392341,-0.0005122,-3.66674E-6,-0.228812
342,11:31:58.278 AM,-0.00392341,-0.0005122,-0.00101962,-0.202795
343,11:31:58.478 AM,-0.00494092,-0.00152882,-0.00101962,-0.137751
344,11:31:58.678 AM,-0.00392341,-0.0005122,-3.66674E-6,-0.176778
345,11:31:58.878 AM,-0.00595844,-0.00152882,-0.00101962,-0.15076
346,11:31:59.078 AM,-0.00494092,-0.0005122,-0.00101962,-0.15076
347,11:31:59.278 AM,-0.00494092,-0.00152882,-3.66674E-6,-0.124743
348,11:31:59.478 AM,-0.00494092,-0.0005122,-0.00101962,-0.15076
349,11:31:59.678 AM,-0.00392341,-0.0005122,-3.66674E-6,-0.163769
350,11:31:59.878 AM,-0.00494092,-0.00152882,-0.00101962,-0.189786
351,11:32:00.078 AM,-0.00494092,-0.0005122,-0.00101962,-0.163769
352,11:32:00.278 AM,-0.00494092,-0.0005122,-3.66674E-6,-0.15076
353,11:32:00.478 AM,-0.00494092,-0.0005122,-3.66674E-6,-0.137751
354,11:32:00.678 AM,-0.00392341,-0.0005122,-0.00101962,-0.163769
355,11:32:00.878 AM,-0.00392341,-0.00152882,-0.00101962,-0.137751
356,11:32:01.078 AM,-0.00494092,-0.00152882,-3.66674E-6,-0.15076
357,11:32:01.278 AM,-0.00392341,-0.00152882,-0.00101962,-0.15076
358,11:32:01.478 AM,-0.00494092,-0.00152882,-0.00101962,-0.124743
359,11:32:01.678 AM,-0.00494092,-0.00254544,-0.00101962,-0.124743
360,11:32:01.878 AM,-0.00494092,-0.0005122,-3.66674E-6,-0.163769
361,11:32:02.078 AM,-0.00494092,-0.00152882,-3.66674E-6,-0.111734
362,11:32:02.278 AM,-0.00494092,-0.0005122,-0.00101962,-0.137751
363,11:32:02.478 AM,-0.00595844,-0.0005122,-3.66674E-6,-0.15076
364,11:32:02.678 AM,-0.00494092,-0.0005122,-0.00101962,-0.137751
365,11:32:02.878 AM,-0.00494092,-0.00152882,-0.00101962,-0.137751
366,11:32:03.078 AM,-0.00494092,-0.0005122,-0.00101962,-0.176778
367,11:32:03.278 AM,-0.00595844,-0.00152882,-3.66674E-6,-0.15076
368,11:32:03.478 AM,-0.00697595,-0.00254544,-0.00101962,-0.0987254
369,11:32:03.678 AM,-0.00595844,-0.00152882,-0.00101962,-0.15076
370,11:32:03.878 AM,-0.00697595,-0.00254544,-0.00101962,-0.0987254
371,11:32:04.078 AM,-0.00697595,-0.00254544,-0.00203558,-0.0857167
372,11:32:04.278 AM,-0.00697595,-0.00356206,-0.00101962,-0.111734
373,11:32:04.478 AM,-0.00799346,-0.00356206,-3.66674E-6,-0.137751
374,11:32:04.678 AM,-0.00799346,-0.00254544,-3.66674E-6,-0.111734
375,11:32:04.878 AM,-0.00799346,-0.00254544,-0.00101962,-0.124743
376,11:32:05.078 AM,-0.00799346,-0.00254544,-0.00101962,-0.176778
377,11:32:05.278 AM,-0.00697595,-0.00254544,-0.00101962,-0.15076
378,11:32:05.478 AM,-0.00697595,-0.00254544,-0.00101962,-0.0857167
379,11:32:05.678 AM,-0.00799346,-0.00254544,-3.66674E-6,-0.124743
380,11:32:05.878 AM,-0.00799346,-0.00152882,-3.66674E-6,-0.215804
381,11:32:06.078 AM,-0.00697595,-0.00152882,-0.00101962,-0.176778
382,11:32:06.278 AM,-0.00697595,-0.00254544,-0.00101962,-0.163769
383,11:32:06.478 AM,-0.00799346,-0.00254544,-0.00101962,-0.163769
384,11:32:06.678 AM,-0.00799346,-0.00254544,-0.00101962,-0.124743
385,11:32:06.878 AM,-0.00799346,-0.00152882,-0.00101962,-0.137751
386,11:32:07.078 AM,-0.00697595,-0.00254544,-0.00101962,-0.202795
387,11:32:07.278 AM,-0.00799346,-0.00254544,-0.00101962,-0.163769
388,11:32:07.478 AM,-0.00697595,-0.00152882,-3.66674E-6,-0.189786
389,11:32:07.678 AM,-0.00799346,-0.00254544,-3.66674E-6,-0.137751
390,11:32:07.878 AM,-0.00799346,-0.00254544,-0.00101962,-0.111734
391,11:32:08.078 AM,-0.00799346,-0.00254544,-0.00101962,-0.111734
392,11:32:08.278 AM,-0.00799346,-0.00254544,-0.00203558,-0.15076
393,11:32:08.478 AM,-0.00697595,-0.00254544,-0.00101962,-0.137751
394,11:32:08.678 AM,-0.00697595,-0.00254544,-0.00101962,-0.111734
395,11:32:08.878 AM,-0.00799346,-0.00254544,-0.00101962,-0.176778
396,11:32:09.078 AM,-0.00799346,-0.00254544,-0.00101962,-0.15076
397,11:32:09.278 AM,-0.00799346,-0.00254544,-0.00101962,-0.15076
398,11:32:09.478 AM,-0.00799346,-0.00254544,-3.66674E-6,-0.111734
399,11:32:09.678 AM,-0.00697595,-0.00254544,-0.00101962,-0.163769
400,11:32:09.878 AM,-0.00799346,-0.00254544,-0.00101962,-0.189786
401,11:32:10.078 AM,-0.00697595,-0.00254544,-0.00101962,-0.163769
402,11:32:10.278 AM,-0.00799346,-0.00152882,-0.00101962,-0.15076
403,11:32:10.478 AM,-0.00799346,-0.00254544,-3.66674E-6,-0.215804
404,11:32:10.678 AM,-0.00697595,-0.00152882,-0.00101962,-0.163769
405,11:32:10.878 AM,-0.00799346,-0.00254544,-0.00101962,-0.189786
406,11:32:11.078 AM,-0.00901098,-0.00254544,-0.00101962,-0.111734
407,11:32:11.278 AM,-0.00901098,-0.00356206,-3.66674E-6,-0.15076
408,11:32:11.478 AM,-0.00901098,-0.00254544,0.00101229,-0.163769
409,11:32:11.678 AM,-0.0100285,-0.00254544,-3.66674E-6,-0.15076
410,11:32:11.878 AM,-0.0100285,-0.00356206,-3.66674E-6,-0.15076
411,11:32:12.078 AM,-0.011046,-0.00356206,-3.66674E-6,-0.137751
412,11:32:12.278 AM,-0.0100285,-0.00457868,-0.00101962,-0.0987254
413,11:32:12.478 AM,-0.011046,-0.00356206,-0.00101962,-0.111734
414,11:32:12.678 AM,-0.011046,-0.00457868,-0.00101962,-0.137751
415,11:32:12.878 AM,-0.011046,-0.00356206,-3.66674E-6,-0.137751
416,11:32:13.078 AM,-0.011046,-0.00356206,-3.66674E-6,-0.072708
417,11:32:13.278 AM,-0.011046,-0.00457868,-0.00101962,-0.072708
418,11:32:13.478 AM,-0.011046,-0.00457868,-0.00101962,-0.0857167
419,11:32:13.678 AM,-0.011046,-0.00457868,-0.00101962,-0.111734
420,11:32:13.878 AM,-0.011046,-0.00457868,-0.00101962,-0.0336819
421,11:32:14.078 AM,-0.0120635,-0.00457868,-3.66674E-6,-0.0596993
422,11:32:14.278 AM,-0.011046,-0.00356206,-0.00101962,-0.124743
423,11:32:14.478 AM,-0.0120635,-0.00356206,-0.00101962,-0.0466906
424,11:32:14.678 AM,-0.0120635,-0.00356206,-3.66674E-6,-0.072708
425,11:32:14.878 AM,-0.011046,-0.00457868,-0.00101962,-0.0466906
426,11:32:15.078 AM,-0.0120635,-0.00457868,-0.00101962,-0.00766449
427,11:32:15.278 AM,-0.0120635,-0.00457868,-0.00101962,-0.0206732
428,11:32:15.478 AM,-0.0120635,-0.00457868,-0.00101962,-0.0336819
429,11:32:15.678 AM,-0.013081,-0.00457868,-0.00101962,-0.0206732
430,11:32:15.878 AM,-0.013081,-0.00457868,-0.00101962,-0.0336819
431,11:32:16.078 AM,-0.013081,-0.00457868,-0.00101962,-0.0336819
432,11:32:16.278 AM,-0.013081,-0.00457868,-0.00101962,-0.0596993
433,11:32:16.478 AM,-0.013081,-0.00457868,-0.00101962,-0.0336819
434,11:32:16.678 AM,-0.0120635,-0.00457868,-3.66674E-6,0.0053442
435,11:32:16.878 AM,-0.0120635,-0.0055953,-3.66674E-6,-0.0206732
436,11:32:17.078 AM,-0.013081,-0.0055953,-0.00101962,-0.00766449
437,11:32:17.278 AM,-0.013081,-0.0055953,-0.00203558,0.0183529
438,11:32:17.478 AM,-0.013081,-0.00457868,-0.00101962,0.0443703
439,11:32:17.678 AM,-0.013081,-0.00457868,-3.66674E-6,-0.00766449
440,11:32:17.878 AM,-0.013081,-0.0055953,-0.00101962,0.0313616
441,11:32:18.078 AM,-0.0120635,-0.0055953,-3.66674E-6,-0.00766449
442,11:32:18.278 AM,-0.0120635,-0.00457868,-3.66674E-6,-0.0336819
443,11:32:18.478 AM,-0.0120635,-0.00457868,-0.00101962,-0.00766449
444,11:32:18.678 AM,-0.013081,-0.00457868,-0.00101962,0.0053442
445,11:32:18.878 AM,-0.0120635,-0.0055953,-3.66674E-6,-0.0336819
446,11:32:19.078 AM,-0.0140985,-0.00457868,-3.66674E-6,-0.00766449
447,11:32:19.278 AM,-0.013081,-0.00356206,-3.66674E-6,0.0183529
448,11:32:19.478 AM,-0.013081,-0.00457868,-0.00101962,0.057379
449,11:32:19.678 AM,-0.013081,-0.00457868,-3.66674E-6,0.0443703
450,11:32:19.878 AM,-0.0151161,-0.00457868,-0.00101962,0.0313616
451,11:32:20.078 AM,-0.0151161,-0.00457868,-0.00101962,0.057379
452,11:32:20.278 AM,-0.0151161,-0.0055953,-3.66674E-6,0.057379
453,11:32:20.478 AM,-0.013081,-0.00457868,-3.66674E-6,0.0833964
454,11:32:20.678 AM,-0.0151161,-0.0055953,-0.00101962,0.0183529
455,11:32:20.878 AM,-0.0140985,-0.00661191,-0.00101962,0.0053442
456,11:32:21.078 AM,-0.0140985,-0.0055953,-3.66674E-6,0.0183529
457,11:32:21.278 AM,-0.0151161,-0.0055953,-0.00101962,0.0313616
458,11:32:21.478 AM,-0.0140985,-0.0055953,-3.66674E-6,0.0443703
459,11:32:21.678 AM,-0.0151161,-0.0055953,-0.00101962,0.0053442
460,11:32:21.878 AM,-0.0151161,-0.0055953,-0.00101962,0.0443703
461,11:32:22.078 AM,-0.0161336,-0.00661191,-0.00101962,0.0833964
462,11:32:22.278 AM,-0.0151161,-0.00457868,-0.00101962,0.0703877
463,11:32:22.478 AM,-0.0151161,-0.0055953,-0.00101962,0.0443703
464,11:32:22.678 AM,-0.0161336,-0.0055953,-0.00101962,0.109414
465,11:32:22.878 AM,-0.0151161,-0.0055953,-0.00101962,0.0703877
466,11:32:23.078 AM,-0.0161336,-0.00661191,-0.00101962,0.0833964
467,11:32:23.278 AM,-0.0161336,-0.0055953,-0.00203558,0.0053442
468,11:32:23.478 AM,-0.0161336,-0.0055953,-3.66674E-6,0.057379
469,11:32:23.678 AM,-0.0161336,-0.00762853,-0.00101962,0.0183529
470,11:32:23.878 AM,-0.0171511,-0.0055953,-0.00101962,0.109414
471,11:32:24.078 AM,-0.0161336,-0.00762853,-0.00101962,0.109414
472,11:32:24.278 AM,-0.0181686,-0.00762853,-0.00101962,0.187466
473,11:32:24.478 AM,-0.0171511,-0.00661191,-3.66674E-6,0.135431
474,11:32:24.678 AM,-0.0181686,-0.00762853,-3.66674E-6,0.174457
475,11:32:24.878 AM,-0.0181686,-0.00661191,-0.00101962,0.200475
476,11:32:25.078 AM,-0.0181686,-0.00864515,-0.00101962,0.226492
477,11:32:25.278 AM,-0.0191861,-0.00762853,-3.66674E-6,0.200475
478,11:32:25.478 AM,-0.0181686,-0.00762853,-0.00101962,0.213483
479,11:32:25.678 AM,-0.0181686,-0.00762853,0.00101229,0.174457
480,11:32:25.878 AM,-0.0181686,-0.00762853,-3.66674E-6,0.161449
481,11:32:26.078 AM,-0.0191861,-0.00661191,-3.66674E-6,0.187466
482,11:32:26.278 AM,-0.0181686,-0.00661191,-0.00101962,0.14844
483,11:32:26.478 AM,-0.0191861,-0.00762853,-3.66674E-6,0.226492
484,11:32:26.678 AM,-0.0191861,-0.00661191,-3.66674E-6,0.187466
485,11:32:26.878 AM,-0.0191861,-0.00864515,-0.00101962,0.187466
486,11:32:27.078 AM,-0.0191861,-0.00762853,-0.00101962,0.239501
487,11:32:27.278 AM,-0.0191861,-0.00661191,-0.00101962,0.187466
488,11:32:27.478 AM,-0.0191861,-0.00864515,-0.00203558,0.252509
489,11:32:27.678 AM,-0.0202036,-0.00762853,-0.00101962,0.239501
490,11:32:27.878 AM,-0.0202036,-0.00762853,-3.66674E-6,0.278527
491,11:32:28.078 AM,-0.0202036,-0.00762853,-0.00101962,0.239501
492,11:32:28.278 AM,-0.0202036,-0.00661191,-0.00101962,0.252509
493,11:32:28.478 AM,-0.0202036,-0.00864515,-3.66674E-6,0.0443703
494,11:32:28.678 AM,-0.0202036,-0.00762853,-0.00101962,0.226492
495,11:32:28.878 AM,-0.0212211,-0.00864515,-3.66674E-6,0.226492
496,11:32:29.078 AM,-0.0202036,-0.00762853,-3.66674E-6,0.252509
497,11:32:29.278 AM,-0.0212211,-0.00864515,-3.66674E-6,0.278527
498,11:32:29.478 AM,-0.0212211,-0.00762853,-0.00203558,0.265518
499,11:32:29.678 AM,-0.0202036,-0.00762853,-3.66674E-6,0.252509
500,11:32:29.878 AM,-0.0212211,-0.00864515,-3.66674E-6,0.278527
501,11:32:30.078 AM,-0.0212211,-0.00864515,-0.00101962,0.239501
502,11:32:30.278 AM,-0.0202036,-0.00864515,-0.00101962,0.213483
503,11:32:30.478 AM,-0.0202036,-0.00762853,-0.00101962,0.239501
504,11:32:30.678 AM,-0.0202036,-0.00864515,-0.00101962,0.252509
505,11:32:30.878 AM,-0.0202036,-0.00762853,-3.66674E-6,0.265518
506,11:32:31.078 AM,-0.0202036,-0.00864515,-0.00101962,0.291536
507,11:32:31.278 AM,-0.0202036,-0.00864515,-3.66674E-6,0.252509
508,11:32:31.478 AM,-0.0202036,-0.00762853,-3.66674E-6,0.213483
509,11:32:31.678 AM,-0.0202036,-0.00762853,0.00101229,0.252509
510,11:32:31.878 AM,-0.0202036,-0.00762853,-0.00101962,0.291536
511,11:32:32.078 AM,-0.0202036,-0.00864515,-3.66674E-6,0.291536
512,11:32:32.278 AM,-0.0202036,-0.00864515,-0.00101962,0.265518
513,11:32:32.478 AM,-0.0212211,-0.00762853,-0.00101962,0.265518
514,11:32:32.678 AM,-0.0212211,-0.00864515,-0.00101962,0.265518
515,11:32:32.878 AM,-0.0202036,-0.00864515,-0.00101962,0.304544
516,11:32:33.078 AM,-0.0212211,-0.00762853,-3.66674E-6,0.252509
517,11:32:33.278 AM,-0.0212211,-0.00864515,-0.00101962,0.265518
518,11:32:33.478 AM,-0.0212211,-0.00762853,-0.00101962,0.291536
519,11:32:33.678 AM,-0.0202036,-0.00762853,-0.00101962,0.265518
520,11:32:33.878 AM,-0.0212211,-0.00864515,-0.00101962,0.278527
521,11:32:34.078 AM,-0.0212211,-0.00864515,-0.00101962,0.304544
522,11:32:34.278 AM,-0.0202036,-0.00762853,-0.00101962,0.291536
523,11:32:34.478 AM,-0.0212211,-0.00762853,-0.00101962,0.252509
524,11:32:34.678 AM,-0.0202036,-0.00762853,-0.00101962,0.291536
525,11:32:34.878 AM,-0.0212211,-0.00762853,-0.00101962,0.252509
526,11:32:35.078 AM,-0.0202036,-0.00864515,-3.66674E-6,0.252509
527,11:32:35.278 AM,-0.0222386,-0.00864515,-0.00101962,0.291536
528,11:32:35.478 AM,-0.0212211,-0.00864515,-0.00101962,0.226492
529,11:32:35.678 AM,-0.0212211,-0.00762853,-0.00101962,0.252509
530,11:32:35.878 AM,-0.0212211,-0.00864515,-0.00101962,0.278527
531,11:32:36.078 AM,-0.0212211,-0.00864515,-0.00101962,0.278527
532,11:32:36.278 AM,-0.0212211,-0.00864515,-3.66674E-6,0.239501
533,11:32:36.478 AM,-0.0212211,-0.00864515,-3.66674E-6,0.265518
534,11:32:36.678 AM,-0.0222386,-0.00762853,-0.00101962,0.291536
535,11:32:36.878 AM,-0.0222386,-0.00864515,-3.66674E-6,0.291536
536,11:32:37.078 AM,-0.0222386,-0.00762853,-0.00101962,0.252509
537,11:32:37.278 AM,-0.0202036,-0.00762853,-3.66674E-6,0.291536
538,11:32:37.478 AM,-0.0212211,-0.00864515,-0.00101962,0.291536
539,11:32:37.678 AM,-0.0222386,-0.00864515,-0.00101962,0.291536
540,11:32:37.878 AM,-0.0212211,-0.00762853,-0.00101962,0.330562
541,11:32:38.078 AM,-0.0212211,-0.00864515,-3.66674E-6,0.291536
542,11:32:38.278 AM,-0.0212211,-0.00864515,-0.00101962,0.291536
543,11:32:38.478 AM,-0.0212211,-0.00762853,-0.00101962,0.278527
544,11:32:38.678 AM,-0.0212211,-0.00864515,-3.66674E-6,0.304544
545,11:32:38.878 AM,-0.0212211,-0.00864515,-0.00101962,0.317553
546,11:32:39.078 AM,-0.0212211,-0.00864515,-3.66674E-6,0.291536
547,11:32:39.278 AM,-0.0202036,-0.00864515,-0.00101962,0.265518
548,11:32:39.478 AM,-0.0202036,-0.00864515,-0.00203558,0.34357
549,11:32:39.678 AM,-0.0202036,-0.00864515,-0.00203558,0.278527
550,11:32:39.878 AM,-0.0212211,-0.00864515,-3.66674E-6,0.278527
551,11:32:40.078 AM,-0.0222386,-0.00864515,-0.00101962,0.239501
552,11:32:40.278 AM,-0.0222386,-0.00864515,-0.00203558,0.265518
553,11:32:40.478 AM,-0.0212211,-0.00864515,-0.00101962,0.278527
554,11:32:40.678 AM,-0.0212211,-0.00864515,-0.00101962,0.317553
555,11:32:40.878 AM,-0.0222386,-0.00762853,-3.66674E-6,0.291536
556,11:32:41.078 AM,-0.0222386,-0.00864515,-0.00101962,0.317553
557,11:32:41.278 AM,-0.0212211,-0.00762853,-3.66674E-6,0.330562
558,11:32:41.478 AM,-0.0222386,-0.00864515,-3.66674E-6,0.34357
559,11:32:41.678 AM,-0.0212211,-0.00864515,-0.00101962,0.356579
560,11:32:41.878 AM,-0.0222386,-0.00864515,-0.00101962,0.369588
561,11:32:42.078 AM,-0.0222386,-0.00864515,-0.00101962,0.34357
562,11:32:42.278 AM,-0.0212211,-0.00864515,-0.00101962,0.317553
563,11:32:42.478 AM,-0.0222386,-0.00864515,-0.00101962,0.330562
564,11:32:42.678 AM,-0.0212211,-0.00864515,-3.66674E-6,0.304544
565,11:32:42.878 AM,-0.0212211,-0.00864515,-0.00101962,0.304544
566,11:32:43.078 AM,-0.0222386,-0.00864515,-3.66674E-6,0.304544
567,11:32:43.278 AM,-0.0222386,-0.00762853,-0.00101962,0.291536
568,11:32:43.478 AM,-0.0212211,-0.00966177,-3.66674E-6,0.330562
569,11:32:43.678 AM,-0.0212211,-0.00864515,-3.66674E-6,0.317553
570,11:32:43.878 AM,-0.0222386,-0.00864515,-0.00101962,0.304544
571,11:32:44.078 AM,-0.0212211,-0.00864515,-0.00101962,0.291536
572,11:32:44.278 AM,-0.0212211,-0.00966177,-0.00101962,0.304544
573,11:32:44.478 AM,-0.0212211,-0.00864515,-3.66674E-6,0.265518
574,11:32:44.678 AM,-0.0212211,-0.00762853,-0.00101962,0.291536
575,11:32:44.878 AM,-0.0222386,-0.00966177,0.00101229,0.330562
576,11:32:45.078 AM,-0.0222386,-0.00864515,-0.00101962,0.278527
577,11:32:45.278 AM,-0.0212211,-0.00762853,-3.66674E-6,0.304544
578,11:32:45.478 AM,-0.0212211,-0.00864515,-0.00101962,0.317553
579,11:32:45.678 AM,-0.0212211,-0.00864515,-0.00101962,0.304544
580,11:32:45.878 AM,-0.0222386,-0.00864515,-3.66674E-6,0.291536
581,11:32:46.078 AM,-0.0222386,-0.00864515,-0.00101962,0.304544
582,11:32:46.278 AM,-0.0222386,-0.00864515,-0.00101962,0.278527
583,11:32:46.478 AM,-0.0212211,-0.00864515,-3.66674E-6,0.291536
584,11:32:46.678 AM,-0.0222386,-0.00864515,-3.66674E-6,0.291536
585,11:32:46.878 AM,-0.0212211,-0.00864515,-0.00203558,0.278527
586,11:32:47.078 AM,-0.0222386,-0.00864515,-0.00101962,0.291536
587,11:32:47.278 AM,-0.0222386,-0.00966177,-0.00101962,0.291536
588,11:32:47.478 AM,-0.0212211,-0.00966177,-0.00101962,0.226492
589,11:32:47.678 AM,-0.0212211,-0.00762853,-0.00101962,0.278527
590,11:32:47.878 AM,-0.0212211,-0.00864515,-0.00101962,0.265518
591,11:32:48.078 AM,-0.0222386,-0.00762853,-3.66674E-6,0.278527
592,11:32:48.278 AM,-0.0222386,-0.00762853,-0.00101962,0.291536
593,11:32:48.478 AM,-0.0222386,-0.00864515,-3.66674E-6,0.239501
594,11:32:48.678 AM,-0.0212211,-0.00864515,-0.00101962,0.291536
595,11:32:48.878 AM,-0.0222386,-0.00864515,-0.00101962,0.278527
596,11:32:49.078 AM,-0.0222386,-0.00864515,-0.00101962,0.304544
597,11:32:49.278 AM,-0.0222386,-0.00762853,-0.00101962,0.317553
598,11:32:49.478 AM,-0.0212211,-0.00864515,-0.00101962,0.239501
599,11:32:49.678 AM,-0.0232562,-0.00864515,-3.66674E-6,0.226492
600,11:32:49.878 AM,-0.0222386,-0.00864515,-0.00101962,0.265518
601,11:32:50.078 AM,-0.0222386,-0.00864515,-0.00101962,0.252509
602,11:32:50.278 AM,-0.0212211,-0.00864515,-0.00101962,0.304544
603,11:32:50.478 AM,-0.0222386,-0.00864515,-0.00101962,0.265518
604,11:32:50.678 AM,-0.0222386,-0.00864515,-3.66674E-6,0.304544
605,11:32:50.878 AM,-0.0222386,-0.00864515,-3.66674E-6,0.291536
606,11:32:51.078 AM,-0.0222386,-0.00864515,-0.00101962,0.252509
607,11:32:51.278 AM,-0.0212211,-0.00864515,-0.00101962,0.252509
608,11:32:51.478 AM,-0.0222386,-0.00864515,-0.00101962,0.252509
609,11:32:51.678 AM,-0.0222386,-0.00864515,-0.00101962,0.265518
610,11:32:51.878 AM,-0.0212211,-0.00864515,-0.00101962,0.265518
611,11:32:52.078 AM,-0.0212211,-0.00864515,-0.00101962,0.291536
612,11:32:52.278 AM,-0.0222386,-0.00864515,-0.00101962,0.265518
613,11:32:52.478 AM,-0.0222386,-0.00966177,-0.00101962,0.239501
614,11:32:52.678 AM,-0.0222386,-0.00762853,-0.00101962,0.278527
615,11:32:52.878 AM,-0.0222386,-0.00864515,-0.00203558,0.200475
616,11:32:53.078 AM,-0.0222386,-0.00864515,-0.00101962,0.291536
617,11:32:53.278 AM,-0.0222386,-0.00864515,-0.00101962,0.291536
618,11:32:53.478 AM,-0.0222386,-0.00864515,-0.00101962,0.317553
619,11:32:53.678 AM,-0.0222386,-0.00864515,-0.00101962,0.304544
620,11:32:53.878 AM,-0.0212211,-0.00864515,-3.66674E-6,0.317553
621,11:32:54.078 AM,-0.0232562,-0.00864515,-0.00101962,0.330562
622,11:32:54.278 AM,-0.0232562,-0.00864515,-3.66674E-6,0.291536
623,11:32:54.478 AM,-0.0232562,-0.00966177,-0.00101962,0.356579
624,11:32:54.678 AM,-0.0242737,-0.00864515,-3.66674E-6,0.395605
625,11:32:54.878 AM,-0.0242737,-0.0106784,-0.00101962,0.408614
626,11:32:55.078 AM,-0.0242737,-0.0106784,-0.00101962,0.434631
627,11:32:55.278 AM,-0.0252912,-0.0106784,-3.66674E-6,0.395605
628,11:32:55.478 AM,-0.0252912,-0.011695,-0.00101962,0.473657
629,11:32:55.678 AM,-0.0273262,-0.0106784,-0.00101962,0.460649
630,11:32:55.878 AM,-0.0283437,-0.0127116,-3.66674E-6,0.421623
631,11:32:56.078 AM,-0.0283437,-0.0127116,-0.00101962,0.44764
632,11:32:56.278 AM,-0.0303787,-0.0127116,-0.00101962,0.499675
633,11:32:56.478 AM,-0.0313963,-0.0137282,-0.00101962,0.525692
634,11:32:56.678 AM,-0.0313963,-0.0137282,-0.00101962,0.551709
635,11:32:56.878 AM,-0.0344488,-0.0147449,-0.00101962,0.64277
636,11:32:57.078 AM,-0.0364838,-0.0157615,-3.66674E-6,0.733831
637,11:32:57.278 AM,-0.0385188,-0.0167781,-0.00101962,0.759849
638,11:32:57.478 AM,-0.0395364,-0.0177947,-0.00101962,0.785866
639,11:32:57.678 AM,-0.0395364,-0.0167781,-0.00101962,0.798875
640,11:32:57.878 AM,-0.0385188,-0.0177947,-3.66674E-6,0.811883
641,11:32:58.078 AM,-0.0395364,-0.0177947,-0.00101962,0.811883
642,11:32:58.278 AM,-0.0395364,-0.0188113,-3.66674E-6,0.798875
643,11:32:58.478 AM,-0.0395364,-0.0177947,-3.66674E-6,0.798875
644,11:32:58.678 AM,-0.0405539,-0.0177947,-0.00101962,0.798875
645,11:32:58.878 AM,-0.0405539,-0.0177947,-0.00101962,0.837901
646,11:32:59.078 AM,-0.0405539,-0.0188113,-3.66674E-6,0.811883
647,11:32:59.278 AM,-0.0405539,-0.0188113,-3.66674E-6,0.824892
648,11:32:59.478 AM,-0.0395364,-0.0177947,-0.00101962,0.811883
649,11:32:59.678 AM,-0.0415714,-0.0177947,-3.66674E-6,0.863918
650,11:32:59.878 AM,-0.0405539,-0.0188113,-3.66674E-6,0.863918
651,11:33:00.078 AM,-0.0415714,-0.0177947,-0.00101962,0.837901
652,11:33:00.278 AM,-0.0405539,-0.0188113,-0.00203558,0.85091
653,11:33:00.478 AM,-0.0405539,-0.0188113,-0.00101962,0.85091
654,11:33:00.678 AM,-0.0415714,-0.0177947,-0.00203558,0.876927
655,11:33:00.878 AM,-0.0415714,-0.0177947,-0.00101962,0.837901
656,11:33:01.078 AM,-0.0415714,-0.0188113,-0.00101962,0.85091
657,11:33:01.278 AM,-0.0415714,-0.0188113,-3.66674E-6,0.889936
658,11:33:01.478 AM,-0.0415714,-0.0188113,-0.00101962,0.811883
659,11:33:01.678 AM,-0.0415714,-0.0188113,-3.66674E-6,0.902944
660,11:33:01.878 AM,-0.0405539,-0.0188113,-0.00101962,0.889936
661,11:33:02.078 AM,-0.0425889,-0.0188113,-3.66674E-6,0.876927
662,11:33:02.278 AM,-0.0415714,-0.0188113,-3.66674E-6,0.876927
663,11:33:02.478 AM,-0.0425889,-0.0188113,-0.00101962,0.837901
664,11:33:02.678 AM,-0.0425889,-0.0188113,-3.66674E-6,0.902944
665,11:33:02.878 AM,-0.0415714,-0.0188113,-0.00101962,0.85091
666,11:33:03.078 AM,-0.0405539,-0.0188113,-3.66674E-6,0.915953
667,11:33:03.278 AM,-0.0425889,-0.0188113,-0.00101962,0.902944
668,11:33:03.478 AM,-0.0415714,-0.0188113,-3.66674E-6,0.902944
669,11:33:03.678 AM,-0.0415714,-0.0188113,-0.00101962,0.902944
670,11:33:03.878 AM,-0.0425889,-0.0188113,-0.00101962,0.902944
671,11:33:04.078 AM,-0.0425889,-0.0188113,-3.66674E-6,0.889936
672,11:33:04.278 AM,-0.0415714,-0.0188113,-0.00101962,0.824892
673,11:33:04.478 AM,-0.0415714,-0.0188113,-0.00203558,0.824892
674,11:33:04.678 AM,-0.0415714,-0.0188113,-0.00101962,0.837901
675,11:33:04.878 AM,-0.0425889,-0.019828,-0.00101962,0.876927
676,11:33:05.078 AM,-0.0425889,-0.0177947,-0.00101962,0.915953
677,11:33:05.278 AM,-0.0436064,-0.0188113,-0.00101962,0.876927
678,11:33:05.478 AM,-0.0425889,-0.0188113,-0.00101962,0.902944
679,11:33:05.678 AM,-0.0425889,-0.0188113,-0.00101962,0.889936
680,11:33:05.878 AM,-0.0425889,-0.0177947,-0.00101962,0.915953
681,11:33:06.078 AM,-0.0415714,-0.0188113,-3.66674E-6,0.902944
682,11:33:06.278 AM,-0.0425889,-0.0188113,-3.66674E-6,0.915953
683,11:33:06.478 AM,-0.0415714,-0.0188113,-3.66674E-6,0.915953
684,11:33:06.678 AM,-0.0425889,-0.0188113,-0.00101962,0.915953
685,11:33:06.878 AM,-0.0415714,-0.0188113,-0.00101962,0.889936
686,11:33:07.078 AM,-0.0425889,-0.0188113,-0.00101962,0.928962
687,11:33:07.278 AM,-0.0425889,-0.019828,-0.00101962,0.876927
688,11:33:07.478 AM,-0.0415714,-0.0188113,-0.00101962,0.902944
689,11:33:07.678 AM,-0.0425889,-0.019828,-0.00101962,0.902944
690,11:33:07.878 AM,-0.0436064,-0.019828,-3.66674E-6,0.902944
691,11:33:08.078 AM,-0.0436064,-0.0188113,-3.66674E-6,0.889936
692,11:33:08.278 AM,-0.0425889,-0.0188113,-3.66674E-6,0.889936
693,11:33:08.478 AM,-0.0425889,-0.019828,-3.66674E-6,0.902944
694,11:33:08.678 AM,-0.0425889,-0.019828,-0.00101962,0.902944
695,11:33:08.878 AM,-0.0436064,-0.0188113,-0.00101962,0.876927
696,11:33:09.078 AM,-0.0425889,-0.0177947,-0.00101962,0.863918
697,11:33:09.278 AM,-0.0436064,-0.019828,-0.00101962,0.876927
698,11:33:09.478 AM,-0.0425889,-0.0188113,-0.00101962,0.902944
699,11:33:09.678 AM,-0.0425889,-0.0188113,-3.66674E-6,0.876927
700,11:33:09.878 AM,-0.0436064,-0.0188113,-3.66674E-6,0.902944
701,11:33:10.078 AM,-0.0436064,-0.0188113,-0.00101962,0.915953
702,11:33:10.278 AM,-0.0425889,-0.0188113,-0.00101962,0.915953
703,11:33:10.478 AM,-0.0436064,-0.0188113,-0.00101962,0.889936
704,11:33:10.678 AM,-0.0436064,-0.0188113,-0.00101962,0.915953
705,11:33:10.878 AM,-0.0436064,-0.0188113,-3.66674E-6,0.915953
706,11:33:11.078 AM,-0.0436064,-0.0188113,-3.66674E-6,0.915953
707,11:33:11.278 AM,-0.0436064,-0.0188113,-0.00101962,0.915953
708,11:33:11.478 AM,-0.0425889,-0.019828,-0.00203558,0.85091
709,11:33:11.678 AM,-0.0436064,-0.019828,-3.66674E-6,0.915953
710,11:33:11.878 AM,-0.0425889,-0.0188113,-3.66674E-6,0.967988
711,11:33:12.078 AM,-0.0425889,-0.0188113,-0.00101962,0.902944
712,11:33:12.278 AM,-0.0436064,-0.0188113,-0.00203558,0.876927
713,11:33:12.478 AM,-0.0436064,-0.0188113,-0.00101962,0.889936
714,11:33:12.678 AM,-0.0436064,-0.0188113,-0.00101962,0.902944
715,11:33:12.878 AM,-0.0436064,-0.019828,-0.00101962,0.902944
716,11:33:13.078 AM,-0.0425889,-0.0188113,-3.66674E-6,0.915953
717,11:33:13.278 AM,-0.0436064,-0.0188113,-3.66674E-6,0.876927
718,11:33:13.478 AM,-0.0436064,-0.0188113,-3.66674E-6,0.876927
719,11:33:13.678 AM,-0.0436064,-0.0188113,-3.66674E-6,0.85091
720,11:33:13.878 AM,-0.0436064,-0.0188113,-0.00101962,0.876927
721,11:33:14.078 AM,-0.0436064,-0.019828,-0.00101962,0.876927
722,11:33:14.278 AM,-0.0436064,-0.019828,-3.66674E-6,0.863918
723,11:33:14.478 AM,-0.0425889,-0.0188113,-0.00101962,0.876927
724,11:33:14.678 AM,-0.0436064,-0.019828,-3.66674E-6,0.85091
725,11:33:14.878 AM,-0.0425889,-0.019828,-3.66674E-6,0.915953
726,11:33:15.078 AM,-0.0436064,-0.0188113,-3.66674E-6,0.889936
727,11:33:15.278 AM,-0.0436064,-0.019828,-0.00203558,0.902944
728,11:33:15.478 AM,-0.0436064,-0.0188113,-0.00101962,0.863918
729,11:33:15.678 AM,-0.0436064,-0.019828,-0.00101962,0.902944
730,11:33:15.878 AM,-0.0425889,-0.0188113,-0.00203558,0.863918
731,11:33:16.078 AM,-0.0436064,-0.0188113,-0.00101962,0.902944
732,11:33:16.278 AM,-0.0436064,-0.019828,-3.66674E-6,0.876927
733,11:33:16.478 AM,-0.0436064,-0.0188113,-0.00203558,0.863918
734,11:33:16.678 AM,-0.0425889,-0.019828,-3.66674E-6,0.915953
735,11:33:16.878 AM,-0.0436064,-0.019828,-0.00101962,0.902944
736,11:33:17.078 AM,-0.0436064,-0.0188113,-0.00101962,0.876927
737,11:33:17.278 AM,-0.0436064,-0.0188113,-0.00101962,0.889936
738,11:33:17.478 AM,-0.0436064,-0.0188113,-0.00101962,0.863918
739,11:33:17.678 AM,-0.0436064,-0.019828,-3.66674E-6,0.85091
740,11:33:17.878 AM,-0.0436064,-0.0188113,-0.00101962,0.876927
741,11:33:18.078 AM,-0.0436064,-0.0188113,-0.00101962,0.915953
742,11:33:18.278 AM,-0.0425889,-0.019828,-3.66674E-6,0.915953
743,11:33:18.478 AM,-0.0436064,-0.0188113,-0.00101962,0.915953
744,11:33:18.678 AM,-0.0436064,-0.0208446,-0.00101962,0.94197
745,11:33:18.878 AM,-0.0436064,-0.0188113,-0.00101962,0.876927
746,11:33:19.078 AM,-0.0436064,-0.0208446,-0.00101962,0.915953
747,11:33:19.278 AM,-0.0436064,-0.019828,-0.00101962,0.902944
748,11:33:19.478 AM,-0.0425889,-0.019828,-3.66674E-6,0.876927
749,11:33:19.678 AM,-0.0436064,-0.0188113,-0.00101962,0.85091
750,11:33:19.878 AM,-0.0436064,-0.0188113,-3.66674E-6,0.889936
751,11:33:20.078 AM,-0.0436064,-0.0188113,-0.00101962,0.837901
752,11:33:20.278 AM,-0.0436064,-0.019828,-0.00101962,0.824892
753,11:33:20.478 AM,-0.0436064,-0.019828,-3.66674E-6,0.811883
754,11:33:20.678 AM,-0.0436064,-0.0188113,-0.00101962,0.837901
755,11:33:20.878 AM,-0.0436064,-0.0177947,-3.66674E-6,0.824892
756,11:33:21.078 AM,-0.0436064,-0.0188113,-3.66674E-6,0.759849
757,11:33:21.278 AM,-0.0436064,-0.019828,-3.66674E-6,0.863918
758,11:33:21.478 AM,-0.0436064,-0.019828,0.00101229,0.798875
759,11:33:21.678 AM,-0.0436064,-0.019828,-3.66674E-6,0.85091
760,11:33:21.878 AM,-0.0446239,-0.0188113,-0.00101962,0.863918
761,11:33:22.078 AM,-0.0436064,-0.019828,-0.00101962,0.837901
762,11:33:22.278 AM,-0.0436064,-0.0188113,-0.00101962,0.876927
763,11:33:22.478 AM,-0.0436064,-0.0188113,-0.00101962,0.876927
764,11:33:22.678 AM,-0.0436064,-0.0177947,-0.00101962,0.902944
765,11:33:22.878 AM,-0.0436064,-0.019828,-0.00101962,0.876927
766,11:33:23.078 AM,-0.0436064,-0.019828,-0.00203558,0.863918
767,11:33:23.278 AM,-0.0436064,-0.019828,-3.66674E-6,0.863918
768,11:33:23.478 AM,-0.0436064,-0.0188113,-3.66674E-6,0.889936
769,11:33:23.678 AM,-0.0436064,-0.019828,0.00101229,0.863918
770,11:33:23.878 AM,-0.0436064,-0.0188113,-3.66674E-6,0.824892
771,11:33:24.078 AM,-0.0436064,-0.019828,-0.00101962,0.889936
772,11:33:24.278 AM,-0.0436064,-0.019828,-0.00101962,0.876927
773,11:33:24.478 AM,-0.0425889,-0.0188113,-0.00101962,0.889936
774,11:33:24.678 AM,-0.0436064,-0.019828,-0.00101962,0.889936
775,11:33:24.878 AM,-0.0425889,-0.019828,-0.00101962,0.889936
776,11:33:25.078 AM,-0.0436064,-0.0188113,-3.66674E-6,0.863918
777,11:33:25.278 AM,-0.0436064,-0.0188113,-3.66674E-6,0.889936
778,11:33:25.478 AM,-0.0436064,-0.019828,-3.66674E-6,0.85091
779,11:33:25.678 AM,-0.0436064,-0.0188113,-3.66674E-6,0.85091
780,11:33:25.878 AM,-0.0436064,-0.019828,-0.00101962,0.876927
781,11:33:26.078 AM,-0.0436064,-0.0188113,-3.66674E-6,0.837901
782,11:33:26.278 AM,-0.0436064,-0.0188113,-3.66674E-6,0.889936
783,11:33:26.478 AM,-0.0436064,-0.019828,-0.00101962,0.876927
784,11:33:26.678 AM,-0.0436064,-0.0208446,-0.00101962,0.876927
785,11:33:26.878 AM,-0.0436064,-0.019828,-3.66674E-6,0.876927
786,11:33:27.078 AM,-0.0436064,-0.0188113,-0.00101962,0.915953
787,11:33:27.278 AM,-0.0436064,-0.0188113,-0.00203558,0.863918
788,11:33:27.478 AM,-0.0436064,-0.019828,-0.00101962,0.863918
789,11:33:27.678 AM,-0.0436064,-0.019828,-0.00101962,0.876927
790,11:33:27.878 AM,-0.0436064,-0.019828,-3.66674E-6,0.876927
791,11:33:28.078 AM,-0.0436064,-0.019828,-3.66674E-6,0.863918
792,11:33:28.278 AM,-0.0436064,-0.019828,-0.00101962,0.889936
793,11:33:28.478 AM,-0.0436064,-0.019828,-3.66674E-6,0.889936
794,11:33:28.678 AM,-0.0436064,-0.019828,-3.66674E-6,0.928962
795,11:33:28.878 AM,-0.0436064,-0.019828,-0.00101962,0.889936
796,11:33:29.078 AM,-0.0436064,-0.019828,-0.00101962,0.824892
797,11:33:29.278 AM,-0.0436064,-0.0188113,-3.66674E-6,0.889936
798,11:33:29.478 AM,-0.0436064,-0.019828,0.00101229,0.902944
799,11:33:29.678 AM,-0.0436064,-0.019828,-0.00101962,0.889936
800,11:33:29.878 AM,-0.0436064,-0.0188113,-0.00101962,0.863918
801,11:33:30.078 AM,-0.0436064,-0.0188113,-0.00101962,0.837901
802,11:33:30.278 AM,-0.0436064,-0.0208446,-3.66674E-6,0.876927
803,11:33:30.478 AM,-0.0436064,-0.0188113,-0.00101962,0.863918
804,11:33:30.678 AM,-0.0436064,-0.0188113,-3.66674E-6,0.837901
805,11:33:30.878 AM,-0.0436064,-0.0188113,-0.00101962,0.863918
806,11:33:31.078 AM,-0.0436064,-0.019828,-3.66674E-6,0.863918
807,11:33:31.278 AM,-0.0436064,-0.0188113,-0.00101962,0.863918
808,11:33:31.478 AM,-0.0436064,-0.019828,-0.00101962,0.824892
809,11:33:31.678 AM,-0.0436064,-0.019828,-3.66674E-6,0.889936
810,11:33:31.878 AM,-0.0436064,-0.019828,-0.00101962,0.876927
811,11:33:32.078 AM,-0.0446239,-0.019828,-3.66674E-6,0.876927
812,11:33:32.278 AM,-0.0446239,-0.019828,-0.00101962,0.824892
813,11:33:32.478 AM,-0.0446239,-0.0188113,-0.00101962,0.902944
814,11:33:32.678 AM,-0.0436064,-0.0188113,-0.00101962,0.863918
815,11:33:32.878 AM,-0.0436064,-0.0188113,-0.00101962,0.837901
816,11:33:33.078 AM,-0.0446239,-0.019828,-0.00101962,0.876927
817,11:33:33.278 AM,-0.0446239,-0.0188113,-3.66674E-6,0.889936
818,11:33:33.478 AM,-0.0436064,-0.019828,-0.00101962,0.889936
819,11:33:33.678 AM,-0.0436064,-0.0188113,-0.00101962,0.889936
820,11:33:33.878 AM,-0.0436064,-0.0188113,-0.00101962,0.94197
821,11:33:34.078 AM,-0.0436064,-0.019828,-0.00203558,0.876927
822,11:33:34.278 AM,-0.0436064,-0.0188113,-0.00101962,0.915953
823,11:33:34.478 AM,-0.0436064,-0.0188113,-0.00101962,0.902944
824,11:33:34.678 AM,-0.0436064,-0.0188113,-3.66674E-6,0.902944
825,11:33:34.878 AM,-0.0436064,-0.0188113,-0.00101962,0.902944
826,11:33:35.078 AM,-0.0436064,-0.0188113,-0.00101962,0.876927
827,11:33:35.278 AM,-0.0446239,-0.019828,-0.00101962,0.902944
828,11:33:35.478 AM,-0.0436064,-0.0208446,-0.00101962,0.876927
829,11:33:35.678 AM,-0.0436064,-0.0188113,-0.00203558,0.902944
830,11:33:35.878 AM,-0.0446239,-0.019828,-0.00101962,0.915953
831,11:33:36.078 AM,-0.0436064,-0.019828,-0.00101962,0.889936
832,11:33:36.278 AM,-0.0436064,-0.0188113,-3.66674E-6,0.876927
833,11:33:36.478 AM,-0.0436064,-0.019828,-0.00101962,0.902944
834,11:33:36.678 AM,-0.0446239,-0.019828,-0.00203558,0.837901
835,11:33:36.878 AM,-0.0446239,-0.0188113,-0.00101962,0.863918
836,11:33:37.078 AM,-0.0436064,-0.0188113,-0.00101962,0.876927
837,11:33:37.278 AM,-0.0436064,-0.0188113,-0.00101962,0.902944
838,11:33:37.478 AM,-0.0436064,-0.0188113,-3.66674E-6,0.863918
839,11:33:37.678 AM,-0.0446239,-0.0188113,-0.00101962,0.915953
840,11:33:37.878 AM,-0.0446239,-0.0188113,-3.66674E-6,0.902944
841,11:33:38.078 AM,-0.0446239,-0.019828,-0.00101962,0.902944
842,11:33:38.278 AM,-0.0446239,-0.0188113,-0.00101962,0.889936
843,11:33:38.478 AM,-0.0446239,-0.0188113,-0.00101962,0.876927
844,11:33:38.678 AM,-0.0436064,-0.0188113,-0.00101962,0.863918
845,11:33:38.878 AM,-0.0436064,-0.019828,-0.00101962,0.863918
846,11:33:39.078 AM,-0.0446239,-0.019828,-3.66674E-6,0.837901
847,11:33:39.278 AM,-0.0446239,-0.019828,-3.66674E-6,0.876927
848,11:33:39.478 AM,-0.0446239,-0.019828,-3.66674E-6,0.889936
849,11:33:39.678 AM,-0.0446239,-0.019828,-3.66674E-6,0.902944
850,11:33:39.878 AM,-0.0436064,-0.0208446,-0.00101962,0.863918
851,11:33:40.078 AM,-0.0436064,-0.019828,-0.00101962,0.902944
852,11:33:40.278 AM,-0.0436064,-0.0188113,-3.66674E-6,0.889936
853,11:33:40.478 AM,-0.0436064,-0.019828,-0.00101962,0.889936
854,11:33:40.678 AM,-0.0436064,-0.019828,-0.00203558,0.863918
855,11:33:40.878 AM,-0.0436064,-0.0188113,-0.00101962,0.902944
856,11:33:41.078 AM,-0.0436064,-0.019828,-0.00101962,0.837901
857,11:33:41.278 AM,-0.0436064,-0.019828,-0.00101962,0.902944
858,11:33:41.478 AM,-0.0436064,-0.0188113,-0.00101962,0.889936
859,11:33:41.678 AM,-0.0436064,-0.019828,-3.66674E-6,0.902944
860,11:33:41.878 AM,-0.0436064,-0.019828,-0.00101962,0.902944
861,11:33:42.078 AM,-0.0436064,-0.0188113,-3.66674E-6,0.902944
862,11:33:42.278 AM,-0.0446239,-0.0188113,-0.00101962,0.915953
863,11:33:42.478 AM,-0.0436064,-0.0188113,-0.00101962,0.876927
864,11:33:42.678 AM,-0.0446239,-0.0188113,-3.66674E-6,0.863918
865,11:33:42.878 AM,-0.0446239,-0.0188113,-0.00101962,0.889936
866,11:33:43.078 AM,-0.0436064,-0.019828,-0.00101962,0.889936
867,11:33:43.278 AM,-0.0436064,-0.019828,-3.66674E-6,0.915953
868,11:33:43.478 AM,-0.0436064,-0.0188113,-0.00101962,0.889936
869,11:33:43.678 AM,-0.0436064,-0.019828,-3.66674E-6,0.889936
870,11:33:43.878 AM,-0.0436064,-0.0188113,-0.00101962,0.876927
871,11:33:44.078 AM,-0.0436064,-0.0188113,-0.00203558,0.915953
872,11:33:44.278 AM,-0.0436064,-0.0188113,-0.00101962,0.889936
873,11:33:44.478 AM,-0.0436064,-0.0188113,-0.00101962,0.889936
874,11:33:44.678 AM,-0.0436064,-0.019828,-0.00101962,0.94197
875,11:33:44.878 AM,-0.0446239,-0.0188113,-0.00101962,0.876927
876,11:33:45.078 AM,-0.0436064,-0.019828,-3.66674E-6,0.876927
877,11:33:45.278 AM,-0.0436064,-0.0188113,-0.00101962,0.915953
878,11:33:45.478 AM,-0.0436064,-0.019828,-3.66674E-6,0.902944
879,11:33:45.678 AM,-0.0446239,-0.019828,-0.00101962,0.863918
880,11:33:45.878 AM,-0.0436064,-0.0188113,-3.66674E-6,0.863918
881,11:33:46.078 AM,-0.0436064,-0.0188113,-0.00101962,0.85091
882,11:33:46.278 AM,-0.0436064,-0.0188113,-3.66674E-6,0.876927
883,11:33:46.478 AM,-0.0446239,-0.019828,-0.00101962,0.863918
884,11:33:46.678 AM,-0.0446239,-0.019828,-0.00101962,0.889936
885,11:33:46.878 AM,-0.0436064,-0.0188113,-3.66674E-6,0.915953
886,11:33:47.078 AM,-0.0436064,-0.0188113,-3.66674E-6,0.889936
887,11:33:47.278 AM,-0.0446239,-0.019828,-3.66674E-6,0.85091
888,11:33:47.478 AM,-0.0446239,-0.019828,-0.00101962,0.824892
889,11:33:47.678 AM,-0.0436064,-0.0188113,-0.00101962,0.889936
890,11:33:47.878 AM,-0.0436064,-0.0208446,-0.00101962,0.915953
891,11:33:48.078 AM,-0.0436064,-0.0188113,-0.00101962,0.863918
892,11:33:48.278 AM,-0.0446239,-0.0188113,-0.00101962,0.863918
893,11:33:48.478 AM,-0.0436064,-0.0188113,-0.00101962,0.902944
894,11:33:48.678 AM,-0.0436064,-0.0188113,-0.00101962,0.85091
895,11:33:48.878 AM,-0.0446239,-0.0188113,-0.00101962,0.876927
896,11:33:49.078 AM,-0.0436064,-0.019828,-0.00101962,0.863918
897,11:33:49.278 AM,-0.0436064,-0.019828,-3.66674E-6,0.876927
898,11:33:49.478 AM,-0.0446239,-0.019828,-3.66674E-6,0.863918
899,11:33:49.678 AM,-0.0436064,-0.019828,-0.00101962,0.85091
900,11:33:49.878 AM,-0.0436064,-0.019828,-0.00101962,0.876927
901,11:33:50.078 AM,-0.0446239,-0.0188113,-3.66674E-6,0.837901
902,11:33:50.278 AM,-0.0446239,-0.019828,-3.66674E-6,0.837901
903,11:33:50.478 AM,-0.0436064,-0.019828,-3.66674E-6,0.876927
904,11:33:50.678 AM,-0.0446239,-0.019828,-0.00101962,0.915953
905,11:33:50.878 AM,-0.0436064,-0.019828,-3.66674E-6,0.902944
906,11:33:51.078 AM,-0.0446239,-0.019828,-0.00101962,0.915953
907,11:33:51.278 AM,-0.0446239,-0.019828,-0.00101962,0.902944
908,11:33:51.478 AM,-0.0436064,-0.019828,-0.00101962,0.915953
909,11:33:51.678 AM,-0.0446239,-0.0188113,-0.00101962,0.889936
910,11:33:51.878 AM,-0.0436064,-0.019828,-0.00101962,0.889936
911,11:33:52.078 AM,-0.0436064,-0.019828,-0.00101962,0.889936
912,11:33:52.278 AM,-0.0436064,-0.0188113,-0.00101962,0.915953
913,11:33:52.478 AM,-0.0446239,-0.0188113,-3.66674E-6,0.915953
914,11:33:52.678 AM,-0.0436064,-0.019828,-3.66674E-6,0.876927
915,11:33:52.878 AM,-0.0436064,-0.0188113,-0.00101962,0.85091
916,11:33:53.078 AM,-0.0436064,-0.0188113,-3.66674E-6,0.902944
917,11:33:53.278 AM,-0.0436064,-0.0188113,-3.66674E-6,0.915953
918,11:33:53.478 AM,-0.0436064,-0.019828,-0.00101962,0.889936
919,11:33:53.678 AM,-0.0436064,-0.019828,-0.00101962,0.876927
920,11:33:53.878 AM,-0.0436064,-0.019828,-3.66674E-6,0.876927
921,11:33:54.078 AM,-0.0446239,-0.019828,-0.00101962,0.902944
922,11:33:54.278 AM,-0.0436064,-0.019828,-0.00101962,0.876927
923,11:33:54.478 AM,-0.0436064,-0.0188113,-3.66674E-6,0.928962
924,11:33:54.678 AM,-0.0436064,-0.0208446,-3.66674E-6,0.889936
925,11:33:54.878 AM,-0.0436064,-0.0208446,-3.66674E-6,0.889936
926,11:33:55.078 AM,-0.0446239,-0.0188113,-0.00203558,0.915953
927,11:33:55.278 AM,-0.0436064,-0.0188113,-0.00101962,0.889936
928,11:33:55.478 AM,-0.0446239,-0.019828,-0.00101962,0.902944
929,11:33:55.678 AM,-0.0436064,-0.019828,-3.66674E-6,0.902944
930,11:33:55.878 AM,-0.0446239,-0.0188113,-3.66674E-6,0.876927
931,11:33:56.078 AM,-0.0446239,-0.0188113,-0.00101962,0.85091
932,11:33:56.278 AM,-0.0436064,-0.0188113,-0.00101962,0.889936
933,11:33:56.478 AM,-0.0446239,-0.019828,-0.00101962,0.915953
934,11:33:56.678 AM,-0.0446239,-0.0188113,-0.00101962,0.85091
935,11:33:56.878 AM,-0.0436064,-0.019828,-0.00101962,0.876927
936,11:33:57.078 AM,-0.0456414,-0.019828,-0.00101962,0.863918
937,11:33:57.278 AM,-0.0446239,-0.019828,-0.00101962,0.811883
938,11:33:57.478 AM,-0.0446239,-0.0188113,-0.00101962,0.863918
939,11:33:57.678 AM,-0.0436064,-0.019828,-0.00101962,0.876927
940,11:33:57.878 AM,-0.0436064,-0.019828,-3.66674E-6,0.876927
941,11:33:58.078 AM,-0.0436064,-0.019828,-3.66674E-6,0.876927
942,11:33:58.278 AM,-0.0436064,-0.019828,-0.00101962,0.889936
943,11:33:58.478 AM,-0.0436064,-0.0188113,-3.66674E-6,0.837901
944,11:33:58.678 AM,-0.0446239,-0.0188113,-3.66674E-6,0.889936
945,11:33:58.878 AM,-0.0436064,-0.019828,-0.00101962,0.889936
946,11:33:59.078 AM,-0.0436064,-0.019828,-0.00101962,0.863918
947,11:33:59.278 AM,-0.0436064,-0.0188113,-0.00203558,0.902944
948,11:33:59.478 AM,-0.0446239,-0.0188113,-0.00101962,0.876927
949,11:33:59.678 AM,-0.0436064,-0.0188113,-0.00101962,0.902944
950,11:33:59.878 AM,-0.0446239,-0.019828,-3.66674E-6,0.889936
951,11:34:00.078 AM,-0.0436064,-0.0188113,-0.00101962,0.863918
952,11:34:00.278 AM,-0.0446239,-0.019828,-0.00101962,0.876927
953,11:34:00.478 AM,-0.0446239,-0.019828,-0.00101962,0.889936
954,11:34:00.678 AM,-0.0436064,-0.019828,-3.66674E-6,0.876927
955,11:34:00.878 AM,-0.0436064,-0.019828,-0.00203558,0.863918
956,11:34:01.078 AM,-0.0436064,-0.019828,-0.00101962,0.863918
957,11:34:01.278 AM,-0.0446239,-0.019828,-0.00101962,0.798875
958,11:34:01.478 AM,-0.0446239,-0.019828,-0.00101962,0.876927
959,11:34:01.678 AM,-0.0436064,-0.019828,-0.00101962,0.863918
960,11:34:01.878 AM,-0.0436064,-0.019828,-0.00101962,0.863918
961,11:34:02.078 AM,-0.0446239,-0.0188113,-0.00101962,0.889936
962,11:34:02.278 AM,-0.0446239,-0.0188113,-0.00101962,0.863918
963,11:34:02.478 AM,-0.0436064,-0.0188113,-0.00101962,0.889936
964,11:34:02.678 AM,-0.0436064,-0.0208446,-0.00101962,0.863918
965,11:34:02.878 AM,-0.0436064,-0.019828,-3.66674E-6,0.94197
966,11:34:03.078 AM,-0.0436064,-0.0188113,-0.00101962,0.863918
967,11:34:03.278 AM,-0.0436064,-0.0188113,-3.66674E-6,0.915953
968,11:34:03.478 AM,-0.0436064,-0.019828,-0.00101962,0.928962
969,11:34:03.678 AM,-0.0446239,-0.019828,-0.00101962,0.889936
970,11:34:03.878 AM,-0.0436064,-0.0208446,-0.00101962,0.902944
971,11:34:04.078 AM,-0.0436064,-0.019828,-0.00203558,0.889936
972,11:34:04.278 AM,-0.0446239,-0.0188113,-0.00101962,0.902944
973,11:34:04.478 AM,-0.0436064,-0.0188113,-3.66674E-6,0.889936
974,11:34:04.678 AM,-0.0436064,-0.0208446,-3.66674E-6,0.902944
975,11:34:04.878 AM,-0.0456414,-0.019828,-0.00101962,0.915953
976,11:34:05.078 AM,-0.0436064,-0.019828,-0.00101962,0.902944
977,11:34:05.278 AM,-0.0436064,-0.019828,-0.00101962,0.928962
978,11:34:05.478 AM,-0.0446239,-0.0188113,-3.66674E-6,0.915953
979,11:34:05.678 AM,-0.0436064,-0.019828,-0.00101962,0.915953
980,11:34:05.878 AM,-0.0436064,-0.019828,-3.66674E-6,0.902944
981,11:34:06.078 AM,-0.0446239,-0.019828,-3.66674E-6,0.928962
982,11:34:06.278 AM,-0.0436064,-0.0188113,-0.00101962,0.928962
983,11:34:06.478 AM,-0.0436064,-0.0188113,-3.66674E-6,0.915953
984,11:34:06.678 AM,-0.0436064,-0.019828,-3.66674E-6,0.954979
985,11:34:06.878 AM,-0.0436064,-0.019828,-3.66674E-6,0.915953
986,11:34:07.078 AM,-0.0436064,-0.0188113,-0.00101962,0.94197
987,11:34:07.278 AM,-0.0456414,-0.019828,-0.00101962,0.915953
988,11:34:07.478 AM,-0.0436064,-0.019828,-3.66674E-6,0.915953
989,11:34:07.678 AM,-0.0436064,-0.019828,-3.66674E-6,0.928962
990,11:34:07.878 AM,-0.0446239,-0.019828,-0.00101962,0.915953
991,11:34:08.078 AM,-0.0446239,-0.019828,-3.66674E-6,0.915953
992,11:34:08.278 AM,-0.0436064,-0.019828,-0.00203558,0.902944
993,11:34:08.478 AM,-0.0446239,-0.019828,-0.00101962,0.889936
994,11:34:08.678 AM,-0.0436064,-0.019828,-3.66674E-6,0.876927
995,11:34:08.878 AM,-0.0436064,-0.019828,-0.00101962,0.915953
996,11:34:09.078 AM,-0.0446239,-0.0188113,0.00101229,0.915953
997,11:34:09.278 AM,-0.0446239,-0.0208446,-0.00101962,0.837901
998,11:34:09.478 AM,-0.0446239,-0.019828,-3.66674E-6,0.928962
999,11:34:09.678 AM,-0.0436064,-0.0188113,-3.66674E-6,0.928962
1000,11:34:09.878 AM,-0.0436064,-0.019828,-0.00101962,0.889936
1001,11:34:10.078 AM,-0.0436064,-0.019828,-3.66674E-6,0.928962
1002,11:34:10.278 AM,-0.0446239,-0.0188113,-0.00101962,0.915953
1003,11:34:10.478 AM,-0.0436064,-0.019828,-0.00101962,0.889936
1004,11:34:10.678 AM,-0.0446239,-0.0188113,-3.66674E-6,0.889936
1005,11:34:10.878 AM,-0.0436064,-0.019828,-3.66674E-6,0.928962
1006,11:34:11.078 AM,-0.0436064,-0.0188113,0.00101229,0.928962
1007,11:34:11.278 AM,-0.0436064,-0.019828,-0.00101962,0.928962
1008,11:34:11.478 AM,-0.0446239,-0.019828,-0.00101962,0.94197
1009,11:34:11.678 AM,-0.0446239,-0.0188113,-3.66674E-6,0.915953
1010,11:34:11.878 AM,-0.0436064,-0.0188113,-0.00101962,0.902944
1011,11:34:12.078 AM,-0.0446239,-0.019828,-0.00101962,0.94197
1012,11:34:12.278 AM,-0.0436064,-0.019828,-0.00101962,0.889936
1013,11:34:12.478 AM,-0.0446239,-0.019828,-3.66674E-6,0.928962
1014,11:34:12.678 AM,-0.0446239,-0.0188113,-0.00101962,0.863918
1015,11:34:12.878 AM,-0.0436064,-0.0188113,-3.66674E-6,0.889936
1016,11:34:13.078 AM,-0.0436064,-0.0188113,-0.00101962,0.876927
1017,11:34:13.278 AM,-0.0436064,-0.0208446,-0.00101962,0.876927
1018,11:34:13.478 AM,-0.0446239,-0.019828,-3.66674E-6,0.889936
1019,11:34:13.678 AM,-0.0446239,-0.019828,-0.00101962,0.85091
1020,11:34:13.878 AM,-0.0446239,-0.0188113,-3.66674E-6,0.876927
1021,11:34:14.078 AM,-0.0436064,-0.0188113,-0.00101962,0.876927
1022,11:34:14.278 AM,-0.0446239,-0.019828,-0.00101962,0.876927
1023,11:34:14.478 AM,-0.0446239,-0.019828,-3.66674E-6,0.824892
1024,11:34:14.678 AM,-0.0436064,-0.0208446,-0.00101962,0.902944
1025,11:34:14.878 AM,-0.0436064,-0.0188113,-0.00101962,0.889936
1026,11:34:15.078 AM,-0.0446239,-0.0188113,-3.66674E-6,0.876927
1027,11:34:15.278 AM,-0.0446239,-0.019828,-0.00101962,0.824892
1028,11:34:15.478 AM,-0.0436064,-0.019828,-0.00101962,0.837901
1029,11:34:15.678 AM,-0.0446239,-0.0208446,-0.00101962,0.811883
1030,11:34:15.878 AM,-0.0436064,-0.0208446,-0.00101962,0.863918
1031,11:34:16.078 AM,-0.0446239,-0.0188113,-0.00101962,0.824892
1032,11:34:16.278 AM,-0.0446239,-0.019828,-0.00101962,0.863918
1033,11:34:16.478 AM,-0.0446239,-0.0208446,-0.00101962,0.902944
1034,11:34:16.678 AM,-0.0436064,-0.0188113,-3.66674E-6,0.863918
1035,11:34:16.878 AM,-0.0446239,-0.019828,-0.00101962,0.837901
1036,11:34:17.078 AM,-0.0436064,-0.0208446,-0.00101962,0.902944
1037,11:34:17.278 AM,-0.0446239,-0.0188113,-3.66674E-6,0.889936
1038,11:34:17.478 AM,-0.0446239,-0.019828,-3.66674E-6,0.863918
1039,11:34:17.678 AM,-0.0446239,-0.0188113,-0.00101962,0.863918
1040,11:34:17.878 AM,-0.0446239,-0.019828,-3.66674E-6,0.863918
1041,11:34:18.078 AM,-0.0446239,-0.0208446,-3.66674E-6,0.876927
1042,11:34:18.278 AM,-0.0446239,-0.019828,-0.00101962,0.863918
1043,11:34:18.478 AM,-0.0436064,-0.019828,-0.00101962,0.889936
1044,11:34:18.678 AM,-0.0446239,-0.0188113,-0.00101962,0.902944
1045,11:34:18.878 AM,-0.0446239,-0.0188113,-0.00101962,0.902944
1046,11:34:19.078 AM,-0.0436064,-0.0188113,-3.66674E-6,0.863918
1047,11:34:19.278 AM,-0.0446239,-0.0208446,-0.00101962,0.876927
1048,11:34:19.478 AM,-0.0436064,-0.0208446,-0.00101962,0.85091
1049,11:34:19.678 AM,-0.0446239,-0.0208446,-0.00101962,0.824892
1050,11:34:19.878 AM,-0.0436064,-0.019828,-3.66674E-6,0.876927
1051,11:34:20.078 AM,-0.0446239,-0.0188113,-0.00101962,0.876927
1052,11:34:20.278 AM,-0.0436064,-0.0208446,-3.66674E-6,0.876927
1053,11:34:20.478 AM,-0.0436064,-0.019828,-3.66674E-6,0.876927
1054,11:34:20.678 AM,-0.0446239,-0.0188113,-3.66674E-6,0.863918
1055,11:34:20.878 AM,-0.0446239,-0.019828,-0.00101962,0.863918
1056,11:34:21.078 AM,-0.0436064,-0.019828,-0.00101962,0.824892
1057,11:34:21.278 AM,-0.0446239,-0.019828,-0.00101962,0.863918
1058,11:34:21.478 AM,-0.0456414,-0.0188113,-0.00101962,0.902944
1059,11:34:21.678 AM,-0.0446239,-0.019828,-0.00101962,0.876927
1060,11:34:21.878 AM,-0.0456414,-0.0188113,-0.00101962,0.902944
1061,11:34:22.078 AM,-0.0446239,-0.019828,-0.00101962,0.902944
1062,11:34:22.278 AM,-0.0446239,-0.0188113,-3.66674E-6,0.876927
1063,11:34:22.478 AM,-0.0436064,-0.019828,-0.00101962,0.915953
1064,11:34:22.678 AM,-0.0446239,-0.0188113,-0.00101962,0.915953
1065,11:34:22.878 AM,-0.0446239,-0.019828,-0.00101962,0.876927
1066,11:34:23.078 AM,-0.0446239,-0.019828,-3.66674E-6,0.915953
1067,11:34:23.278 AM,-0.0446239,-0.0208446,-0.00101962,0.889936
1068,11:34:23.478 AM,-0.0436064,-0.019828,0.00101229,0.915953
1069,11:34:23.678 AM,-0.0436064,-0.019828,-0.00101962,0.915953
1070,11:34:23.878 AM,-0.0446239,-0.0188113,-0.00101962,0.889936
1071,11:34:24.078 AM,-0.0446239,-0.0208446,-3.66674E-6,0.915953
1072,11:34:24.278 AM,-0.0436064,-0.019828,-0.00203558,0.811883
1073,11:34:24.478 AM,-0.0446239,-0.019828,-3.66674E-6,0.889936
1074,11:34:24.678 AM,-0.0446239,-0.0188113,-0.00101962,0.915953
1075,11:34:24.878 AM,-0.0446239,-0.019828,-0.00101962,0.928962
1076,11:34:25.078 AM,-0.0436064,-0.0188113,-3.66674E-6,0.954979
1077,11:34:25.278 AM,-0.0446239,-0.0188113,-0.00101962,0.928962
1078,11:34:25.478 AM,-0.0436064,-0.019828,-3.66674E-6,0.967988
1079,11:34:25.678 AM,-0.0446239,-0.0188113,-3.66674E-6,0.94197
1080,11:34:25.878 AM,-0.0436064,-0.019828,-3.66674E-6,0.928962
1081,11:34:26.078 AM,-0.0446239,-0.0188113,-3.66674E-6,0.928962
1082,11:34:26.278 AM,-0.0446239,-0.019828,-0.00101962,0.954979
1083,11:34:26.478 AM,-0.0456414,-0.019828,-3.66674E-6,0.94197
1084,11:34:26.678 AM,-0.0446239,-0.0188113,-3.66674E-6,0.928962
1085,11:34:26.878 AM,-0.0446239,-0.019828,-0.00101962,0.915953
1086,11:34:27.078 AM,-0.0446239,-0.0188113,-0.00101962,0.928962
1087,11:34:27.278 AM,-0.0436064,-0.0188113,-3.66674E-6,0.94197
1088,11:34:27.478 AM,-0.0446239,-0.019828,-0.00101962,0.928962
1089,11:34:27.678 AM,-0.0436064,-0.0208446,-0.00101962,0.915953
1090,11:34:27.878 AM,-0.0446239,-0.019828,-0.00101962,0.915953
1091,11:34:28.078 AM,-0.0446239,-0.0208446,-3.66674E-6,0.902944
1092,11:34:28.278 AM,-0.0436064,-0.0188113,-3.66674E-6,0.915953
1093,11:34:28.478 AM,-0.0436064,-0.019828,-0.00101962,0.863918
1094,11:34:28.678 AM,-0.0446239,-0.019828,-0.00101962,0.876927
1095,11:34:28.878 AM,-0.0446239,-0.0188113,-0.00101962,0.889936
1096,11:34:29.078 AM,-0.0446239,-0.019828,-3.66674E-6,0.889936
1097,11:34:29.278 AM,-0.0436064,-0.0188113,-0.00101962,0.902944
1098,11:34:29.478 AM,-0.0436064,-0.0208446,-0.00101962,0.889936
1099,11:34:29.678 AM,-0.0436064,-0.019828,-3.66674E-6,0.928962
1100,11:34:29.878 AM,-0.0456414,-0.0188113,-0.00101962,0.915953
1101,11:34:30.078 AM,-0.0436064,-0.019828,-0.00101962,0.902944
1102,11:34:30.278 AM,-0.0446239,-0.019828,-0.00101962,0.915953
1103,11:34:30.478 AM,-0.0446239,-0.0208446,-0.00101962,0.863918
1104,11:34:30.678 AM,-0.0446239,-0.019828,-0.00101962,0.889936
1105,11:34:30.878 AM,-0.0446239,-0.019828,-0.00101962,0.837901
1106,11:34:31.078 AM,-0.0446239,-0.019828,-0.00101962,0.876927
1107,11:34:31.278 AM,-0.0446239,-0.0208446,-0.00101962,0.85091
1108,11:34:31.478 AM,-0.0436064,-0.019828,-0.00101962,0.824892
1109,11:34:31.678 AM,-0.0436064,-0.019828,-0.00101962,0.863918
1110,11:34:31.878 AM,-0.0446239,-0.019828,-0.00101962,0.876927
1111,11:34:32.078 AM,-0.0446239,-0.019828,-0.00101962,0.876927
1112,11:34:32.278 AM,-0.0436064,-0.0188113,-0.00101962,0.876927
1113,11:34:32.478 AM,-0.0446239,-0.019828,-3.66674E-6,0.876927
1114,11:34:32.678 AM,-0.0446239,-0.019828,-3.66674E-6,0.837901
1115,11:34:32.878 AM,-0.0446239,-0.0208446,-3.66674E-6,0.889936
1116,11:34:33.078 AM,-0.0446239,-0.0208446,0.00101229,0.889936
1117,11:34:33.278 AM,-0.0446239,-0.0188113,0.00101229,0.85091
1118,11:34:33.478 AM,-0.0446239,-0.0188113,-0.00101962,0.889936
1119,11:34:33.678 AM,-0.0446239,-0.0188113,-3.66674E-6,0.837901
1120,11:34:33.878 AM,-0.0446239,-0.019828,-3.66674E-6,0.889936
1121,11:34:34.078 AM,-0.0446239,-0.019828,-0.00101962,0.876927
1122,11:34:34.278 AM,-0.0436064,-0.019828,-0.00101962,0.902944
1123,11:34:34.478 AM,-0.0446239,-0.019828,-0.00101962,0.824892
1124,11:34:34.678 AM,-0.0436064,-0.019828,-0.00101962,0.811883
1125,11:34:34.878 AM,-0.0446239,-0.0188113,-3.66674E-6,0.85091
1126,11:34:35.078 AM,-0.0446239,-0.0188113,-0.00101962,0.85091
1127,11:34:35.278 AM,-0.0436064,-0.0208446,-0.00101962,0.876927
1128,11:34:35.478 AM,-0.0436064,-0.019828,-0.00101962,0.863918
1129,11:34:35.678 AM,-0.0436064,-0.019828,-0.00101962,0.85091
1130,11:34:35.878 AM,-0.0446239,-0.0188113,-0.00101962,0.889936
1131,11:34:36.078 AM,-0.0436064,-0.019828,-0.00101962,0.876927
1132,11:34:36.278 AM,-0.0446239,-0.019828,-0.00203558,0.876927
1133,11:34:36.478 AM,-0.0446239,-0.019828,-3.66674E-6,0.863918
1134,11:34:36.678 AM,-0.0446239,-0.0188113,-0.00101962,0.876927
1135,11:34:36.878 AM,-0.0446239,-0.019828,-0.00101962,0.876927
1136,11:34:37.078 AM,-0.0446239,-0.019828,0.00101229,0.915953
1137,11:34:37.278 AM,-0.0446239,-0.019828,-3.66674E-6,0.876927
1138,11:34:37.478 AM,-0.0446239,-0.019828,-3.66674E-6,0.837901
1139,11:34:37.678 AM,-0.0456414,-0.019828,-0.00101962,0.863918
1140,11:34:37.878 AM,-0.0436064,-0.019828,-0.00101962,0.863918
1141,11:34:38.078 AM,-0.0436064,-0.0188113,-0.00101962,0.902944
1142,11:34:38.278 AM,-0.0446239,-0.019828,-3.66674E-6,0.902944
1143,11:34:38.478 AM,-0.0446239,-0.019828,-0.00101962,0.889936
1144,11:34:38.678 AM,-0.0436064,-0.019828,-0.00101962,0.94197
1145,11:34:38.878 AM,-0.0446239,-0.019828,-3.66674E-6,0.954979
1146,11:34:39.078 AM,-0.0446239,-0.019828,-0.00101962,0.94197
1147,11:34:39.278 AM,-0.0436064,-0.0208446,-3.66674E-6,0.967988
1148,11:34:39.478 AM,-0.0436064,-0.019828,-0.00101962,0.94197
1149,11:34:39.678 AM,-0.0446239,-0.019828,-0.00101962,0.889936
1150,11:34:39.878 AM,-0.0446239,-0.019828,-0.00101962,0.928962
1151,11:34:40.078 AM,-0.0436064,-0.019828,-0.00101962,0.915953
1152,11:34:40.278 AM,-0.0436064,-0.019828,-0.00101962,0.915953
1153,11:34:40.478 AM,-0.0446239,-0.019828,-3.66674E-6,0.889936
1154,11:34:40.678 AM,-0.0436064,-0.0208446,-3.66674E-6,0.954979
1155,11:34:40.878 AM,-0.0436064,-0.019828,-0.00101962,0.915953
1156,11:34:41.078 AM,-0.0436064,-0.019828,-0.00101962,0.94197
1157,11:34:41.278 AM,-0.0446239,-0.019828,-0.00101962,0.863918
1158,11:34:41.478 AM,-0.0446239,-0.0208446,-0.00101962,0.902944
1159,11:34:41.678 AM,-0.0436064,-0.019828,-3.66674E-6,0.915953
1160,11:34:41.878 AM,-0.0436064,-0.019828,-0.00101962,0.915953
1161,11:34:42.078 AM,-0.0436064,-0.0208446,-3.66674E-6,0.94197
1162,11:34:42.278 AM,-0.0446239,-0.019828,-0.00101962,0.876927
1163,11:34:42.478 AM,-0.0446239,-0.019828,-0.00101962,0.915953
1164,11:34:42.678 AM,-0.0436064,-0.0208446,-3.66674E-6,0.928962
1165,11:34:42.878 AM,-0.0446239,-0.019828,-0.00101962,0.94197
1166,11:34:43.078 AM,-0.0436064,-0.019828,-0.00203558,0.928962
1167,11:34:43.278 AM,-0.0446239,-0.0188113,-3.66674E-6,0.954979
1168,11:34:43.478 AM,-0.0446239,-0.019828,-0.00101962,0.915953
1169,11:34:43.678 AM,-0.0446239,-0.019828,-0.00203558,0.94197
1170,11:34:43.878 AM,-0.0446239,-0.019828,-0.00101962,0.889936
1171,11:34:44.078 AM,-0.0446239,-0.0208446,-0.00101962,0.928962
1172,11:34:44.278 AM,-0.0446239,-0.019828,-3.66674E-6,0.928962
1173,11:34:44.478 AM,-0.0446239,-0.0208446,-0.00101962,0.915953
1174,11:34:44.678 AM,-0.0446239,-0.0208446,-0.00101962,0.889936
1175,11:34:44.878 AM,-0.0436064,-0.019828,-0.00101962,0.876927
1176,11:34:45.078 AM,-0.0436064,-0.019828,-3.66674E-6,0.902944
1177,11:34:45.278 AM,-0.0436064,-0.019828,-3.66674E-6,0.928962
1178,11:34:45.478 AM,-0.0446239,-0.0208446,-0.00101962,0.889936
1179,11:34:45.678 AM,-0.0446239,-0.019828,-0.00101962,0.876927
1180,11:34:45.878 AM,-0.0425889,-0.019828,-0.00101962,0.915953
1181,11:34:46.078 AM,-0.0446239,-0.019828,-0.00101962,0.915953
1182,11:34:46.278 AM,-0.0436064,-0.019828,-0.00203558,0.902944
1183,11:34:46.478 AM,-0.0446239,-0.0188113,-0.00101962,0.876927
1184,11:34:46.678 AM,-0.0446239,-0.0188113,-0.00101962,0.863918
1185,11:34:46.878 AM,-0.0436064,-0.0208446,-3.66674E-6,0.915953
1186,11:34:47.078 AM,-0.0456414,-0.0188113,-3.66674E-6,0.889936
1187,11:34:47.278 AM,-0.0436064,-0.019828,-3.66674E-6,0.902944
1188,11:34:47.478 AM,-0.0436064,-0.019828,-3.66674E-6,0.915953
1189,11:34:47.678 AM,-0.0446239,-0.019828,-0.00101962,0.876927
1190,11:34:47.878 AM,-0.0436064,-0.0208446,-0.00101962,0.915953
1191,11:34:48.078 AM,-0.0436064,-0.019828,0.00101229,0.889936
1192,11:34:48.278 AM,-0.0436064,-0.019828,-0.00101962,0.915953
1193,11:34:48.478 AM,-0.0436064,-0.0208446,-0.00101962,0.902944
1194,11:34:48.678 AM,-0.0446239,-0.019828,-3.66674E-6,0.902944
1195,11:34:48.878 AM,-0.0446239,-0.019828,-3.66674E-6,0.837901
1196,11:34:49.078 AM,-0.0436064,-0.0188113,-0.00101962,0.876927
1197,11:34:49.278 AM,-0.0436064,-0.019828,-0.00101962,0.824892
1198,11:34:49.478 AM,-0.0446239,-0.019828,-0.00101962,0.876927
1199,11:34:49.678 AM,-0.0446239,-0.0208446,-0.00101962,0.876927
1200,11:34:49.878 AM,-0.0436064,-0.0188113,-0.00101962,0.902944
1201,11:34:50.078 AM,-0.0446239,-0.019828,-3.66674E-6,0.889936
1202,11:34:50.278 AM,-0.0446239,-0.019828,-0.00101962,0.928962
1203,11:34:50.478 AM,-0.0446239,-0.019828,-0.00101962,0.915953
1204,11:34:50.678 AM,-0.0446239,-0.019828,-0.00101962,0.915953
1205,11:34:50.878 AM,-0.0436064,-0.019828,-0.00101962,0.915953
1206,11:34:51.078 AM,-0.0446239,-0.019828,-0.00101962,0.902944
1207,11:34:51.278 AM,-0.0436064,-0.019828,-3.66674E-6,0.915953
1208,11:34:51.478 AM,-0.0436064,-0.0188113,-0.00101962,0.915953
1209,11:34:51.678 AM,-0.0446239,-0.019828,-0.00101962,0.954979
1210,11:34:51.878 AM,-0.0446239,-0.019828,-3.66674E-6,0.967988
1211,11:34:52.078 AM,-0.0446239,-0.0208446,-0.00101962,0.902944
1212,11:34:52.278 AM,-0.0436064,-0.019828,-0.00101962,0.94197
1213,11:34:52.478 AM,-0.0436064,-0.019828,-3.66674E-6,0.954979
1214,11:34:52.678 AM,-0.0446239,-0.0208446,-3.66674E-6,0.915953
1215,11:34:52.878 AM,-0.0446239,-0.0188113,-0.00101962,0.915953
1216,11:34:53.078 AM,-0.0436064,-0.019828,-0.00101962,0.915953
1217,11:34:53.278 AM,-0.0446239,-0.0188113,-3.66674E-6,0.889936
1218,11:34:53.478 AM,-0.0446239,-0.0188113,-0.00101962,0.876927
1219,11:34:53.678 AM,-0.0436064,-0.0208446,-0.00101962,0.928962
1220,11:34:53.878 AM,-0.0446239,-0.019828,-0.00101962,0.928962
1221,11:34:54.078 AM,-0.0446239,-0.0188113,-0.00101962,0.902944
1222,11:34:54.278 AM,-0.0436064,-0.0208446,-0.00101962,0.837901
1223,11:34:54.478 AM,-0.0436064,-0.019828,-0.00101962,0.85091
1224,11:34:54.678 AM,-0.0446239,-0.019828,-0.00101962,0.85091
1225,11:34:54.878 AM,-0.0436064,-0.019828,-0.00101962,0.863918
1226,11:34:55.078 AM,-0.0436064,-0.0208446,-3.66674E-6,0.837901
1227,11:34:55.278 AM,-0.0446239,-0.0188113,-0.00101962,0.85091
1228,11:34:55.478 AM,-0.0456414,-0.0208446,-3.66674E-6,0.902944
1229,11:34:55.678 AM,-0.0446239,-0.0188113,-0.00101962,0.94197
1230,11:34:55.878 AM,-0.0446239,-0.0208446,-0.00101962,0.915953
1231,11:34:56.078 AM,-0.0446239,-0.019828,-0.00101962,0.928962
1232,11:34:56.278 AM,-0.0446239,-0.0188113,-0.00101962,0.889936
1233,11:34:56.478 AM,-0.0436064,-0.019828,-0.00101962,0.94197
1234,11:34:56.678 AM,-0.0436064,-0.019828,-3.66674E-6,0.876927
1235,11:34:56.878 AM,-0.0436064,-0.019828,-0.00101962,0.902944
1236,11:34:57.078 AM,-0.0446239,-0.019828,-0.00101962,0.889936
1237,11:34:57.278 AM,-0.0446239,-0.0188113,-3.66674E-6,0.863918
1238,11:34:57.478 AM,-0.0446239,-0.0208446,-0.00101962,0.876927
1239,11:34:57.678 AM,-0.0446239,-0.019828,-3.66674E-6,0.876927
1240,11:34:57.878 AM,-0.0436064,-0.019828,-0.00101962,0.824892
1241,11:34:58.078 AM,-0.0436064,-0.019828,-0.00101962,0.863918
1242,11:34:58.278 AM,-0.0446239,-0.019828,-3.66674E-6,0.889936
1243,11:34:58.478 AM,-0.0436064,-0.0188113,-0.00101962,0.928962
1244,11:34:58.678 AM,-0.0436064,-0.019828,-0.00101962,0.902944
1245,11:34:58.878 AM,-0.0446239,-0.0188113,-0.00101962,0.915953
1246,11:34:59.078 AM,-0.0446239,-0.019828,-0.00101962,0.902944
1247,11:34:59.278 AM,-0.0446239,-0.0188113,-3.66674E-6,0.915953
1248,11:34:59.478 AM,-0.0446239,-0.019828,-3.66674E-6,0.94197
1249,11:34:59.678 AM,-0.0446239,-0.0188113,-3.66674E-6,0.94197
1250,11:34:59.878 AM,-0.0446239,-0.0188113,-3.66674E-6,0.94197
1251,11:35:00.078 AM,-0.0446239,-0.019828,-0.00101962,0.889936
1252,11:35:00.278 AM,-0.0456414,-0.0208446,-0.00101962,0.902944
1253,11:35:00.478 AM,-0.0446239,-0.019828,-0.00101962,0.915953
1254,11:35:00.678 AM,-0.0446239,-0.019828,-0.00101962,0.889936
1255,11:35:00.878 AM,-0.0446239,-0.0188113,-3.66674E-6,0.889936
1256,11:35:01.078 AM,-0.0446239,-0.0208446,-0.00203558,0.889936
1257,11:35:01.278 AM,-0.0436064,-0.019828,-0.00101962,0.915953
1258,11:35:01.478 AM,-0.0446239,-0.0208446,-3.66674E-6,0.94197
1259,11:35:01.678 AM,-0.0446239,-0.019828,-0.00101962,0.915953
1260,11:35:01.878 AM,-0.0446239,-0.0188113,-0.00101962,0.889936
1261,11:35:02.078 AM,-0.0436064,-0.0208446,-0.00101962,0.902944
1262,11:35:02.278 AM,-0.0446239,-0.0208446,-0.00101962,0.889936
1263,11:35:02.478 AM,-0.0446239,-0.0188113,-0.00101962,0.928962
1264,11:35:02.678 AM,-0.0456414,-0.019828,-3.66674E-6,0.928962
1265,11:35:02.878 AM,-0.0446239,-0.019828,-0.00101962,0.928962
1266,11:35:03.078 AM,-0.0446239,-0.0188113,-3.66674E-6,0.928962
1267,11:35:03.278 AM,-0.0446239,-0.0188113,-3.66674E-6,0.928962
1268,11:35:03.478 AM,-0.0446239,-0.0188113,-3.66674E-6,0.967988
1269,11:35:03.678 AM,-0.0446239,-0.019828,-3.66674E-6,0.954979
1270,11:35:03.878 AM,-0.0446239,-0.019828,-0.00101962,0.915953
1271,11:35:04.078 AM,-0.0446239,-0.019828,-3.66674E-6,0.954979
1272,11:35:04.278 AM,-0.0446239,-0.019828,-3.66674E-6,0.902944
1273,11:35:04.478 AM,-0.0436064,-0.0188113,-0.00101962,0.94197
1274,11:35:04.678 AM,-0.0446239,-0.0208446,-0.00203558,0.889936
1275,11:35:04.878 AM,-0.0446239,-0.0188113,-3.66674E-6,0.94197
1276,11:35:05.078 AM,-0.0436064,-0.019828,-3.66674E-6,0.928962
1277,11:35:05.278 AM,-0.0446239,-0.019828,-0.00101962,0.94197
1278,11:35:05.478 AM,-0.0446239,-0.0188113,-0.00101962,0.902944
1279,11:35:05.678 AM,-0.0446239,-0.0188113,-3.66674E-6,0.915953
1280,11:35:05.878 AM,-0.0446239,-0.0188113,-3.66674E-6,0.902944
1281,11:35:06.078 AM,-0.0446239,-0.019828,-0.00101962,0.902944
1282,11:35:06.278 AM,-0.0446239,-0.0188113,-3.66674E-6,0.915953
1283,11:35:06.478 AM,-0.0446239,-0.0188113,-0.00101962,0.928962
1284,11:35:06.678 AM,-0.0446239,-0.019828,-0.00101962,0.915953
1285,11:35:06.878 AM,-0.0436064,-0.019828,-0.00101962,0.915953
1286,11:35:07.078 AM,-0.0446239,-0.019828,-0.00101962,0.954979
1287,11:35:07.278 AM,-0.0446239,-0.0208446,-0.00101962,0.915953
1288,11:35:07.478 AM,-0.0446239,-0.019828,-0.00101962,0.928962
1289,11:35:07.678 AM,-0.0446239,-0.0188113,-0.00101962,0.876927
1290,11:35:07.878 AM,-0.0436064,-0.019828,-0.00101962,0.876927
1291,11:35:08.078 AM,-0.0446239,-0.0208446,-3.66674E-6,0.915953
1292,11:35:08.278 AM,-0.0446239,-0.019828,-3.66674E-6,0.915953
1293,11:35:08.478 AM,-0.0436064,-0.0208446,-0.00101962,0.915953
1294,11:35:08.678 AM,-0.0446239,-0.0188113,-0.00101962,0.889936
1295,11:35:08.878 AM,-0.0436064,-0.0208446,-0.00101962,0.876927
1296,11:35:09.078 AM,-0.0446239,-0.019828,-0.00101962,0.889936
1297,11:35:09.278 AM,-0.0436064,-0.0188113,-0.00101962,0.94197
1298,11:35:09.478 AM,-0.0446239,-0.019828,-0.00101962,0.902944
1299,11:35:09.678 AM,-0.0446239,-0.0188113,-0.00101962,0.915953
1300,11:35:09.878 AM,-0.0446239,-0.019828,-3.66674E-6,0.928962
1301,11:35:10.078 AM,-0.0446239,-0.019828,-3.66674E-6,0.902944
1302,11:35:10.278 AM,-0.0446239,-0.019828,-3.66674E-6,0.928962
1303,11:35:10.478 AM,-0.0446239,-0.0188113,-0.00101962,0.889936
1304,11:35:10.678 AM,-0.0436064,-0.019828,-3.66674E-6,0.915953
1305,11:35:10.878 AM,-0.0446239,-0.019828,-0.00101962,0.967988
1306,11:35:11.078 AM,-0.0436064,-0.019828,-0.00101962,0.902944
1307,11:35:11.278 AM,-0.0446239,-0.019828,-0.00101962,0.928962
1308,11:35:11.478 AM,-0.0446239,-0.019828,-0.00101962,0.889936
1309,11:35:11.678 AM,-0.0446239,-0.0188113,-0.00101962,0.889936
1310,11:35:11.878 AM,-0.0456414,-0.019828,-3.66674E-6,0.967988
1311,11:35:12.078 AM,-0.0446239,-0.0208446,-0.00101962,0.928962
1312,11:35:12.278 AM,-0.0446239,-0.0208446,-3.66674E-6,0.915953
1313,11:35:12.478 AM,-0.0446239,-0.019828,-0.00101962,0.94197
1314,11:35:12.678 AM,-0.0436064,-0.019828,-3.66674E-6,0.928962
1315,11:35:12.878 AM,-0.0446239,-0.019828,-3.66674E-6,0.94197
1316,11:35:13.078 AM,-0.0446239,-0.0208446,-0.00101962,0.902944
1317,11:35:13.278 AM,-0.0446239,-0.0208446,-0.00101962,0.902944
1318,11:35:13.478 AM,-0.0436064,-0.019828,-0.00101962,0.902944
1319,11:35:13.678 AM,-0.0436064,-0.019828,-0.00101962,0.928962
1320,11:35:13.878 AM,-0.0436064,-0.0208446,-3.66674E-6,0.94197
1321,11:35:14.078 AM,-0.0436064,-0.019828,-3.66674E-6,0.954979
1322,11:35:14.278 AM,-0.0446239,-0.019828,-0.00101962,0.94197
1323,11:35:14.478 AM,-0.0436064,-0.019828,-3.66674E-6,0.954979
1324,11:35:14.678 AM,-0.0446239,-0.019828,-0.00101962,0.967988
1325,11:35:14.878 AM,-0.0446239,-0.019828,-0.00101962,0.967988
1326,11:35:15.078 AM,-0.0446239,-0.019828,-0.00101962,0.94197
1327,11:35:15.278 AM,-0.0446239,-0.0208446,-0.00101962,0.94197
1328,11:35:15.478 AM,-0.0446239,-0.0188113,-0.00101962,0.967988
1329,11:35:15.678 AM,-0.0446239,-0.019828,-0.00101962,0.954979
1330,11:35:15.878 AM,-0.0436064,-0.019828,-0.00101962,0.928962
1331,11:35:16.078 AM,-0.0456414,-0.019828,-0.00101962,0.928962
1332,11:35:16.278 AM,-0.0436064,-0.0188113,-3.66674E-6,0.954979
1333,11:35:16.478 AM,-0.0446239,-0.0208446,-0.00101962,0.94197
1334,11:35:16.678 AM,-0.0436064,-0.019828,-0.00101962,0.954979
1335,11:35:16.878 AM,-0.0446239,-0.019828,-0.00101962,0.94197
1336,11:35:17.078 AM,-0.0446239,-0.0208446,-3.66674E-6,0.915953
1337,11:35:17.278 AM,-0.0436064,-0.0208446,-3.66674E-6,0.915953
1338,11:35:17.478 AM,-0.0446239,-0.019828,-3.66674E-6,0.915953
1339,11:35:17.678 AM,-0.0456414,-0.019828,-0.00101962,0.954979
1340,11:35:17.878 AM,-0.0436064,-0.019828,-3.66674E-6,0.928962
1341,11:35:18.078 AM,-0.0456414,-0.0208446,-0.00101962,0.980996
1342,11:35:18.278 AM,-0.0446239,-0.0208446,-0.00101962,0.967988
1343,11:35:18.478 AM,-0.0446239,-0.019828,-0.00101962,0.928962
1344,11:35:18.678 AM,-0.0446239,-0.019828,-3.66674E-6,0.94197
1345,11:35:18.878 AM,-0.0436064,-0.0188113,-0.00101962,0.967988
1346,11:35:19.078 AM,-0.0456414,-0.019828,-0.00101962,0.967988
1347,11:35:19.278 AM,-0.0446239,-0.019828,-0.00101962,0.967988
1348,11:35:19.478 AM,-0.0446239,-0.0208446,-0.00101962,0.980996
1349,11:35:19.678 AM,-0.0446239,-0.0208446,-3.66674E-6,0.954979
1350,11:35:19.878 AM,-0.0446239,-0.019828,-0.00101962,0.94197
1351,11:35:20.078 AM,-0.0446239,-0.0208446,-0.00101962,0.928962
1352,11:35:20.278 AM,-0.0436064,-0.0208446,-3.66674E-6,0.94197
1353,11:35:20.478 AM,-0.0446239,-0.019828,-0.00101962,0.915953
1354,11:35:20.678 AM,-0.0456414,-0.019828,-0.00101962,0.915953
1355,11:35:20.878 AM,-0.0446239,-0.0208446,-0.00101962,0.94197
1356,11:35:21.078 AM,-0.0446239,-0.019828,-0.00101962,0.954979
1357,11:35:21.278 AM,-0.0446239,-0.0188113,-3.66674E-6,0.967988
1358,11:35:21.478 AM,-0.0446239,-0.019828,-0.00101962,0.94197
1359,11:35:21.678 AM,-0.0436064,-0.0208446,-0.00101962,0.967988
1360,11:35:21.878 AM,-0.0446239,-0.0188113,-3.66674E-6,0.967988
1361,11:35:22.078 AM,-0.0446239,-0.019828,-0.00101962,0.928962
1362,11:35:22.278 AM,-0.0436064,-0.0208446,-0.00101962,0.967988
1363,11:35:22.478 AM,-0.0446239,-0.0208446,-3.66674E-6,0.94197
1364,11:35:22.678 AM,-0.0446239,-0.0188113,-0.00101962,0.967988
1365,11:35:22.878 AM,-0.0436064,-0.019828,-0.00101962,0.954979
1366,11:35:23.078 AM,-0.0446239,-0.019828,-0.00101962,0.94197
1367,11:35:23.278 AM,-0.0446239,-0.019828,-3.66674E-6,0.928962
1368,11:35:23.478 AM,-0.0446239,-0.019828,-0.00101962,0.915953
1369,11:35:23.678 AM,-0.0446239,-0.019828,-3.66674E-6,0.954979
1370,11:35:23.878 AM,-0.0436064,-0.019828,-3.66674E-6,0.928962
1371,11:35:24.078 AM,-0.0446239,-0.0208446,-0.00101962,0.928962
1372,11:35:24.278 AM,-0.0436064,-0.019828,0.00101229,0.889936
1373,11:35:24.478 AM,-0.0436064,-0.0208446,-3.66674E-6,0.928962
1374,11:35:24.678 AM,-0.0446239,-0.019828,-0.00101962,0.954979
1375,11:35:24.878 AM,-0.0446239,-0.0208446,-3.66674E-6,0.928962
1376,11:35:25.078 AM,-0.0436064,-0.0188113,-0.00101962,0.94197
1377,11:35:25.278 AM,-0.0446239,-0.019828,-3.66674E-6,0.928962
1378,11:35:25.478 AM,-0.0446239,-0.019828,-0.00203558,0.889936
1379,11:35:25.678 AM,-0.0456414,-0.0188113,-3.66674E-6,0.915953
1380,11:35:25.878 AM,-0.0446239,-0.019828,-0.00101962,0.876927
1381,11:35:26.078 AM,-0.0446239,-0.019828,-0.00101962,0.902944
1382,11:35:26.278 AM,-0.0446239,-0.019828,-3.66674E-6,0.863918
1383,11:35:26.478 AM,-0.0446239,-0.019828,-3.66674E-6,0.876927
1384,11:35:26.678 AM,-0.0436064,-0.0188113,-0.00203558,0.889936
1385,11:35:26.878 AM,-0.0446239,-0.0208446,-3.66674E-6,0.74684
1386,11:35:27.078 AM,-0.0436064,-0.0208446,-0.00101962,0.863918
1387,11:35:27.278 AM,-0.0446239,-0.0188113,-3.66674E-6,0.902944
1388,11:35:27.478 AM,-0.0446239,-0.019828,-3.66674E-6,0.863918
1389,11:35:27.678 AM,-0.0436064,-0.0208446,-3.66674E-6,0.837901
1390,11:35:27.878 AM,-0.0446239,-0.019828,-0.00101962,0.928962
1391,11:35:28.078 AM,-0.0436064,-0.019828,-3.66674E-6,0.876927
1392,11:35:28.278 AM,-0.0436064,-0.0188113,-0.00101962,0.889936
1393,11:35:28.478 AM,-0.0436064,-0.019828,-3.66674E-6,0.902944
1394,11:35:28.678 AM,-0.0456414,-0.0208446,-0.00101962,0.876927
1395,11:35:28.878 AM,-0.0436064,-0.0188113,-0.00101962,0.889936
1396,11:35:29.078 AM,-0.0436064,-0.0188113,-3.66674E-6,0.902944
1397,11:35:29.278 AM,-0.0436064,-0.0208446,-0.00101962,0.876927
1398,11:35:29.478 AM,-0.0436064,-0.019828,-0.00101962,0.915953
1399,11:35:29.678 AM,-0.0446239,-0.019828,-0.00203558,0.85091
1400,11:35:29.878 AM,-0.0446239,-0.0208446,-0.00101962,0.902944
1401,11:35:30.078 AM,-0.0436064,-0.0188113,-0.00101962,0.915953
1402,11:35:30.278 AM,-0.0446239,-0.019828,-3.66674E-6,0.902944
1403,11:35:30.478 AM,-0.0446239,-0.0208446,-0.00101962,0.876927
1404,11:35:30.678 AM,-0.0446239,-0.0208446,-0.00101962,0.889936
1405,11:35:30.878 AM,-0.0436064,-0.019828,-0.00101962,0.94197
1406,11:35:31.078 AM,-0.0446239,-0.0208446,-0.00101962,0.902944
1407,11:35:31.278 AM,-0.0466589,-0.0208446,-0.00101962,0.915953
1408,11:35:31.478 AM,-0.048694,-0.0238944,-3.66674E-6,1.03303
1409,11:35:31.678 AM,-0.054799,-0.0249111,-0.00101962,1.16312
1410,11:35:31.878 AM,-0.0588691,-0.0289775,-3.66674E-6,1.29321
1411,11:35:32.078 AM,-0.0639567,-0.0299942,-0.00101962,1.42329
1412,11:35:32.278 AM,-0.0659917,-0.033044,-0.00101962,1.50134
1413,11:35:32.478 AM,-0.0680267,-0.0350772,-0.00101962,1.54037
1414,11:35:32.678 AM,-0.0710793,-0.0350772,-0.00101962,1.61842
1415,11:35:32.878 AM,-0.0720968,-0.0371105,-3.66674E-6,1.61842
1416,11:35:33.078 AM,-0.0731143,-0.0371105,-0.00101962,1.64444
1417,11:35:33.278 AM,-0.0741318,-0.0371105,-3.66674E-6,1.70948
1418,11:35:33.478 AM,-0.0761668,-0.0381271,-0.00101962,1.76152
1419,11:35:33.678 AM,-0.0782018,-0.0401603,-0.00101962,1.68347
1420,11:35:33.878 AM,-0.0792194,-0.0401603,-0.00101962,1.86559
1421,11:35:34.078 AM,-0.0812544,-0.041177,-0.00101962,1.90461
1422,11:35:34.278 AM,-0.0843069,-0.0432102,-0.00101962,1.98267
1423,11:35:34.478 AM,-0.0863419,-0.0462601,-0.00101962,2.04771
1424,11:35:34.678 AM,-0.088377,-0.0462601,-3.66674E-6,2.06072
1425,11:35:34.878 AM,-0.0914295,-0.0482933,-0.00101962,2.24284
1426,11:35:35.078 AM,-0.0914295,-0.0472767,-0.00101962,2.22983
1427,11:35:35.278 AM,-0.0914295,-0.0482933,-0.00101962,2.22983
1428,11:35:35.478 AM,-0.0914295,-0.0472767,-3.66674E-6,2.25585
1429,11:35:35.678 AM,-0.092447,-0.0482933,-0.00101962,2.24284
1430,11:35:35.878 AM,-0.0914295,-0.0482933,-0.00101962,2.25585
1431,11:35:36.078 AM,-0.092447,-0.0482933,-3.66674E-6,2.22983
1432,11:35:36.278 AM,-0.092447,-0.0482933,-3.66674E-6,2.24284
1433,11:35:36.478 AM,-0.0914295,-0.0482933,-0.00101962,2.20381
1434,11:35:36.678 AM,-0.0934645,-0.0482933,-0.00101962,2.20381
1435,11:35:36.878 AM,-0.092447,-0.0482933,-0.00101962,2.21682
1436,11:35:37.078 AM,-0.0934645,-0.0482933,-0.00101962,2.21682
1437,11:35:37.278 AM,-0.0934645,-0.0482933,-0.00101962,2.19081
1438,11:35:37.478 AM,-0.092447,-0.0482933,-3.66674E-6,2.21682
1439,11:35:37.678 AM,-0.092447,-0.0482933,-3.66674E-6,2.21682
1440,11:35:37.878 AM,-0.092447,-0.0482933,-0.00101962,2.22983
1441,11:35:38.078 AM,-0.0934645,-0.0493099,-0.00101962,2.20381
1442,11:35:38.278 AM,-0.0934645,-0.0493099,-0.00101962,2.26886
1443,11:35:38.478 AM,-0.092447,-0.0482933,-0.00101962,2.21682
1444,11:35:38.678 AM,-0.092447,-0.0493099,-0.00101962,2.25585
1445,11:35:38.878 AM,-0.0934645,-0.0503265,-0.00101962,2.22983
1446,11:35:39.078 AM,-0.092447,-0.0493099,-0.00101962,2.1778
1447,11:35:39.278 AM,-0.0934645,-0.0472767,-0.00101962,2.25585
1448,11:35:39.478 AM,-0.092447,-0.0493099,-0.00101962,2.24284
1449,11:35:39.678 AM,-0.0934645,-0.0482933,-0.00101962,2.24284
1450,11:35:39.878 AM,-0.0934645,-0.0493099,-3.66674E-6,2.26886
1451,11:35:40.078 AM,-0.092447,-0.0482933,-0.00101962,2.19081
1452,11:35:40.278 AM,-0.0934645,-0.0493099,-0.00101962,2.25585
1453,11:35:40.478 AM,-0.0934645,-0.0482933,-3.66674E-6,2.26886
1454,11:35:40.678 AM,-0.0934645,-0.0493099,-3.66674E-6,2.26886
1455,11:35:40.878 AM,-0.094482,-0.0493099,-3.66674E-6,2.24284
1456,11:35:41.078 AM,-0.0934645,-0.0493099,-0.00101962,2.26886
1457,11:35:41.278 AM,-0.0934645,-0.0493099,-3.66674E-6,2.24284
1458,11:35:41.478 AM,-0.0934645,-0.0482933,-0.00101962,2.26886
1459,11:35:41.678 AM,-0.0934645,-0.0493099,-0.00101962,2.25585
1460,11:35:41.878 AM,-0.0934645,-0.0493099,-0.00101962,2.28187
1461,11:35:42.078 AM,-0.0954996,-0.0493099,-0.00101962,2.26886
1462,11:35:42.278 AM,-0.094482,-0.0482933,-0.00101962,2.15178
1463,11:35:42.478 AM,-0.094482,-0.0493099,-0.00203558,2.21682
1464,11:35:42.678 AM,-0.094482,-0.0493099,-0.00101962,2.28187
1465,11:35:42.878 AM,-0.094482,-0.0493099,-0.00101962,2.26886
1466,11:35:43.078 AM,-0.0954996,-0.0493099,-3.66674E-6,2.28187
1467,11:35:43.278 AM,-0.094482,-0.0482933,-0.00101962,2.32089
1468,11:35:43.478 AM,-0.094482,-0.0493099,-3.66674E-6,2.29487
1469,11:35:43.678 AM,-0.094482,-0.0482933,-3.66674E-6,2.30788
1470,11:35:43.878 AM,-0.094482,-0.0493099,-0.00101962,2.26886
1471,11:35:44.078 AM,-0.094482,-0.0482933,-3.66674E-6,2.3339
1472,11:35:44.278 AM,-0.094482,-0.0472767,-0.00101962,2.26886
1473,11:35:44.478 AM,-0.094482,-0.0482933,-0.00101962,2.28187
1474,11:35:44.678 AM,-0.0954996,-0.0482933,-0.00101962,2.29487
1475,11:35:44.878 AM,-0.094482,-0.0493099,-0.00101962,2.26886
1476,11:35:45.078 AM,-0.0954996,-0.0493099,-0.00101962,2.32089
1477,11:35:45.278 AM,-0.094482,-0.0482933,-0.00101962,2.29487
1478,11:35:45.478 AM,-0.094482,-0.0482933,-0.00101962,2.25585
1479,11:35:45.678 AM,-0.0954996,-0.0493099,-3.66674E-6,2.26886
1480,11:35:45.878 AM,-0.094482,-0.0482933,-3.66674E-6,2.29487
1481,11:35:46.078 AM,-0.0954996,-0.0493099,-3.66674E-6,2.21682
1482,11:35:46.278 AM,-0.094482,-0.0503265,-0.00101962,2.28187
1483,11:35:46.478 AM,-0.094482,-0.0493099,-0.00101962,2.21682
1484,11:35:46.678 AM,-0.094482,-0.0493099,-0.00101962,2.21682
1485,11:35:46.878 AM,-0.0954996,-0.0493099,-0.00101962,2.25585
1486,11:35:47.078 AM,-0.0954996,-0.0493099,-0.00203558,2.25585
1487,11:35:47.278 AM,-0.094482,-0.0493099,-0.00203558,2.24284
1488,11:35:47.478 AM,-0.0954996,-0.0493099,-3.66674E-6,2.22983
1489,11:35:47.678 AM,-0.094482,-0.0493099,-0.00101962,2.26886
1490,11:35:47.878 AM,-0.0954996,-0.0493099,-0.00101962,2.29487
1491,11:35:48.078 AM,-0.094482,-0.0493099,-3.66674E-6,2.28187
1492,11:35:48.278 AM,-0.094482,-0.0493099,-0.00101962,2.32089
1493,11:35:48.478 AM,-0.094482,-0.0493099,-0.00101962,2.28187
1494,11:35:48.678 AM,-0.094482,-0.0493099,-3.66674E-6,2.29487
1495,11:35:48.878 AM,-0.094482,-0.0493099,-3.66674E-6,2.28187
1496,11:35:49.078 AM,-0.0954996,-0.0503265,-0.00101962,2.34691
1497,11:35:49.278 AM,-0.0954996,-0.0493099,-0.00101962,2.32089
1498,11:35:49.478 AM,-0.0954996,-0.0482933,-3.66674E-6,2.29487
1499,11:35:49.678 AM,-0.094482,-0.0493099,-0.00101962,2.29487
1500,11:35:49.878 AM,-0.0954996,-0.0482933,-3.66674E-6,2.32089
1501,11:35:50.078 AM,-0.0954996,-0.0493099,-3.66674E-6,2.29487
1502,11:35:50.278 AM,-0.0954996,-0.0493099,-0.00101962,2.30788
1503,11:35:50.478 AM,-0.094482,-0.0493099,-0.00101962,2.3339
1504,11:35:50.678 AM,-0.0954996,-0.0493099,-0.00101962,2.32089
1505,11:35:50.878 AM,-0.094482,-0.0493099,-0.00101962,2.30788
1506,11:35:51.078 AM,-0.0954996,-0.0493099,-0.00101962,2.29487
1507,11:35:51.278 AM,-0.0954996,-0.0493099,-0.00101962,2.32089
1508,11:35:51.478 AM,-0.0954996,-0.0482933,-3.66674E-6,2.32089
1509,11:35:51.678 AM,-0.0954996,-0.0482933,-0.00101962,2.25585
1510,11:35:51.878 AM,-0.094482,-0.0493099,-3.66674E-6,2.32089
1511,11:35:52.078 AM,-0.094482,-0.0493099,-3.66674E-6,2.3339
1512,11:35:52.278 AM,-0.094482,-0.0503265,-0.00101962,2.38594
1513,11:35:52.478 AM,-0.0954996,-0.0482933,-0.00101962,2.38594
1514,11:35:52.678 AM,-0.094482,-0.0482933,-0.00101962,2.3339
1515,11:35:52.878 AM,-0.0954996,-0.0493099,-0.00101962,2.35992
1516,11:35:53.078 AM,-0.0954996,-0.0493099,-0.00101962,2.38594
1517,11:35:53.278 AM,-0.0954996,-0.0493099,-3.66674E-6,2.35992
1518,11:35:53.478 AM,-0.094482,-0.0493099,-0.00101962,2.32089
1519,11:35:53.678 AM,-0.0954996,-0.0482933,-3.66674E-6,2.32089
1520,11:35:53.878 AM,-0.094482,-0.0493099,-0.00101962,2.3339
1521,11:35:54.078 AM,-0.0954996,-0.0493099,-0.00101962,2.3339
1522,11:35:54.278 AM,-0.0954996,-0.0482933,-0.00101962,2.28187
1523,11:35:54.478 AM,-0.094482,-0.0493099,-0.00101962,2.29487
1524,11:35:54.678 AM,-0.0954996,-0.0493099,-0.00101962,2.25585
1525,11:35:54.878 AM,-0.0954996,-0.0493099,-0.00101962,2.28187
1526,11:35:55.078 AM,-0.094482,-0.0493099,-3.66674E-6,2.25585
1527,11:35:55.278 AM,-0.094482,-0.0493099,-3.66674E-6,2.21682
1528,11:35:55.478 AM,-0.094482,-0.0493099,-0.00101962,2.26886
1529,11:35:55.678 AM,-0.094482,-0.0493099,-0.00101962,2.25585
1530,11:35:55.878 AM,-0.0954996,-0.0503265,-0.00101962,2.26886
1531,11:35:56.078 AM,-0.0954996,-0.0493099,-3.66674E-6,2.26886
1532,11:35:56.278 AM,-0.094482,-0.0493099,-0.00101962,2.26886
1533,11:35:56.478 AM,-0.094482,-0.0493099,-3.66674E-6,2.25585
1534,11:35:56.678 AM,-0.0965171,-0.0493099,-0.00101962,2.25585
1535,11:35:56.878 AM,-0.0954996,-0.0482933,-3.66674E-6,2.26886
1536,11:35:57.078 AM,-0.0954996,-0.0503265,-0.00101962,2.28187
1537,11:35:57.278 AM,-0.0954996,-0.0493099,-3.66674E-6,2.26886
1538,11:35:57.478 AM,-0.0954996,-0.0503265,-0.00101962,2.25585
1539,11:35:57.678 AM,-0.0954996,-0.0482933,-3.66674E-6,2.30788
1540,11:35:57.878 AM,-0.0954996,-0.0493099,-3.66674E-6,2.24284
1541,11:35:58.078 AM,-0.0954996,-0.0493099,-0.00101962,2.25585
1542,11:35:58.278 AM,-0.0954996,-0.0503265,-3.66674E-6,2.26886
1543,11:35:58.478 AM,-0.094482,-0.0493099,-0.00101962,2.29487
1544,11:35:58.678 AM,-0.094482,-0.0493099,-0.00101962,2.25585
1545,11:35:58.878 AM,-0.0954996,-0.0493099,-0.00101962,2.30788
1546,11:35:59.078 AM,-0.094482,-0.0482933,-0.00101962,2.28187
1547,11:35:59.278 AM,-0.0954996,-0.0493099,-0.00101962,2.29487
1548,11:35:59.478 AM,-0.0954996,-0.0482933,-3.66674E-6,2.29487
1549,11:35:59.678 AM,-0.0954996,-0.0493099,-0.00203558,2.29487
1550,11:35:59.878 AM,-0.094482,-0.0482933,-3.66674E-6,2.29487
1551,11:36:00.078 AM,-0.0954996,-0.0493099,-3.66674E-6,2.28187
1552,11:36:00.278 AM,-0.094482,-0.0493099,-0.00101962,2.30788
1553,11:36:00.478 AM,-0.0954996,-0.0482933,-0.00101962,2.29487
1554,11:36:00.678 AM,-0.0954996,-0.0503265,-3.66674E-6,2.30788
1555,11:36:00.878 AM,-0.094482,-0.0493099,-3.66674E-6,2.29487
1556,11:36:01.078 AM,-0.0965171,-0.0503265,-3.66674E-6,2.29487
1557,11:36:01.278 AM,-0.0954996,-0.0493099,-3.66674E-6,2.30788
1558,11:36:01.478 AM,-0.094482,-0.0493099,-0.00101962,2.30788
1559,11:36:01.678 AM,-0.0954996,-0.0493099,-0.00101962,2.28187
1560,11:36:01.878 AM,-0.094482,-0.0493099,-3.66674E-6,2.26886
1561,11:36:02.078 AM,-0.0965171,-0.0493099,-0.00101962,2.28187
1562,11:36:02.278 AM,-0.0954996,-0.0503265,-0.00101962,2.29487
1563,11:36:02.478 AM,-0.0965171,-0.0503265,-3.66674E-6,2.32089
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

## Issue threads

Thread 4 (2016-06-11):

Fin redesign

Joedang, 2016-06-11:
The current fin frames (the physical ones) are not the right design. This gives us an opportunity to improve the design before trying to make new ones.

The planform we originally **intended** on making is actually pretty good. The main thing that would be nice to redesign is the manufacturing of the frames. Machining them out of a single block of aluminum on an 11-axis mahine certainly makes a robust product, but it's also the most brute force method imaginable. It would be better to have a design that can be machined in-house on a 2-axis or 3-axis machine (maybe using "sticks" of aluminum for the edges and bolting/registering them into the flange).

If anyone wants to mess with the [OpenRocket models](https://github.com/psas/sw-cad-airframe-lv3.0/tree/master/simulation/ORK), please do. The main criteria for a "good" launch are 0.2 calibers (or more) off the rail, 2 or 3 calibers in flight, and about a degree of coning in the angle of attack. The fins also need to fit on a single module (no longer than 24", preferably less than 18"), and "probably not" be the first thing to hit the ground when the rocket lands.

Closed 2016-09-21.

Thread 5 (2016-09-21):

Machining fin jigs

Joedang, 2016-09-21:
The fin jigs ([middle](../tree/master/cad/finCan/fin_jig_mid.SLDPRT) and [ends](../tree/master/cad/finCan/fin_jig_top_bottom2.SLDPRT)) are designed, but need a few things to come into meatspace.
- [x] There needs to be a 2D technical drawing made of the part. (Not strictly necessary, but VERY handy.)
- [X] The aluminum plates must be acquired.
- [X] There needs to be CAM done for the particular machine it will be made on.
- [X] Someone needs to do the actual machining.
_That's Peter._
- [X] A 1/16" cutter must be purchased. (2 flutes strongly preferred)

This part requires a 1/16th inch end mill and is roughly 18 inches square, I think. It's designed as a purely 2D part.

petermccloud, 2017-04-09:
@Joedang I've been shopping cutters and there are no 1/16" cutters that have a 1/4" shank (since my machine only takes 1/4" and 1/2" shanks). The smallest cutter size for a 1/4" shank is 1/8". So we either need to do this on a different machine or re-design the part.

Joedang, 2017-04-09:
Some of the cutters [here](http://www.2linc.com/endmills/endmills_ballnose_1-16.htm), [here](http://www.2linc.com/endmills_aluminum_2fl_std.htm), and [here](http://www.2linc.com/endmills_aluminum_1fl_std.htm) fit our needs. There's also [this listing](http://www.ebay.com/itm/Kyocera-T0625O188-3F-Square-End-Mill-0-0625-1-16in-Dia-1-4in-Shank-AX-Coated-/332042057753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) on ebay, but I'm not sure how well 3 flutes would work with aluminum when it's that small.

petermccloud, 2017-04-10:
Awesome, thanks for finding this. Got the bits ordered, they should show up on Thursday.

Joedang, 2017-05-21:
Reason for closing: @petermccloud made the thing.

Closed 2017-05-21.

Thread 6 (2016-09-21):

Fin Frame Machining

Joedang, 2016-09-21:
The following things need to complete the fin frames:
- [X] CAM for the particular machine used.
- [X] Machining the profiles of the frames.
- [X] Figure out how to accurately machine those "knife edge" chamfers in 1/8" aluminum.
- [X] Machining the leading/trailing edges.

This is mostly a 2D part. The leading and trailing edges have chamfers. The materials and chamfer mill have already been purchased.

([CAD](../tree/master/cad/finCan/LongFinFiles/LongFins_ALedge.SLDPRT) and [technical drawing](../tree/master/cad/finCan/LongFinFiles/LongFins_ALedge.SLDDRW) )

Joedang, 2017-05-21:
Reason for closing: @petermccloud and @paperman5 made the thing.

Closed 2017-05-21.

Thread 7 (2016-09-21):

Fixing and Machining the Rail Sled

Joedang, 2016-09-21:
This task doesn't have anyone associated with it, and is open to anyone willing to do some machining.

Remaining tasks:
- [X] Tweak the dimensions of the rail sled to better fit the rail.
- [X] Remake the HDPE layers.
- [X] Determine the appropriate thickness of the aluminum base.
- [X] Remake the aluminum base.
- [X] Confirm loose fit with the rail.
_requires a small amount of 3-in-1 oil_
- [X] Machine a second set of parts for the upper sled.

This is a series of 2D parts that bolt together. They could be done on a 2-axis CNC mill or a manual mill with a rotary table and perhaps a DRO. It's three layers of HDPE and one layer of aluminum.

A prototype for the rail sled has already been made, but the dimensions were off and there were some issues with the surface finish of the aluminum base. This would be a good project for an ME undergrad or anyone with access to a machine shop.

The [CAD files are here](../tree/master/cad/railSled), along with the CAM used to machine the prototype. There should be plenty of suitable aluminum and HDPE in the rocket room for this.

JacobTiller, 2017-01-18:
I've updated the cad files (with solid works files and drawings) and pushed them to Git.  I have also made a prototype in the machine shop on a manual mill.  The part needs to be checked out to see if it needs any tweaking before I build the second one.

Joedang, 2017-04-06:
With that little bit of oil, it seemed to slide pretty well. I'd say go ahead with the second one.

Joedang, 2017-05-21:
Reason for closing: @JacobTiller made the thing.

Closed 2017-05-21.

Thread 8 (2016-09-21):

Nose Cone Hardware

Joedang, 2016-09-21:
Some aluminum pieces of the nose cone need to be machined. Things which affect the go/no-go are in **bold**.

Remaining tasks:
- Technical drawings
  - [X] nose tip
  - [X] nose plug
    - [X] needs to be revised/reviewed to match the mold
  - [X] dummy tip
- [X] Acquire the bar stock
- CAM -- _Actually, these all ended up being manually machined._
  - [X] nose tip
  - [ ] nose plug
  - [ ] dummy tip
- Machining/MFG
  - [X] nose tip
  - [ ] nose plug
  - [X] **nose mold**
  - [X] **nose body**
  - [X] dummy tip
  - [X] integration

These are both axially symmetric parts to be turned on a lathe. Their profiles include curves, so they will need to be done on a CNC lathe.

The CAD for these parts [can be found here](../tree/master/cad/nose).
[tip drawing](https://github.com/psas/lv3.0-airframe/blob/master/cad/nose/von_karmon_nose_tip2.pdf)

Joedang, 2017-04-06:
## Current Status
@alexkazam made the CAD + drawing for the tip and preliminary CAD for the plug. He did CAM and started machining but then got distracted by a capstone or something (geez, what a slacker). The in-progress part is... somewhere, lol.

@jschalk is now handling the machining. The fastener/thread size is not specified in the part or the drawing, so someone (most likely @Joedang or @alexkazam) will need to figure out what that was. It would also be worth figuring out if they make Helicoils that size. Maybe you can look that up and we'll just use that, @jschalk.

Joedang, 2017-10-07:
# Update:
@SaturnVF1 machined two dees nuts (formerly "nose plugs") and a tip. Both turned out really well, so I'd say those don't need to be CNC'd on LV4 or other rockets.

The tip was machined in piece-wise sections and smoothed with a file (?) and sand paper. (Maybe @SaturnVF1 can comment on specifics.)

The dee nut was also done on a manual lathe. The inside was hollowed out using a custom-ground HSS cutter, and the outside was knurled for better adhesion into the nosecone.

# Future issues (?):
It would be nice to have procedures in `doc/mfg/` on how to make a nose tip and dee nut using a manual lathe, so people will be able to do it for LV4. @SaturnVF1, if you want to write that, that would be awesome.

# Reason for closing
The nosecone _is a thing_ at this point. It needs some sanding to look presentable, but it's flyable.

Closed 2017-10-07.

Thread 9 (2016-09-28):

Sanding

Joedang, 2016-09-28:
Although we have enough modules for a whole airframe at this point, they all have a rough surface. The outer adhesive covering needs to be sanded to ~1500 grit. This is mostly a warm-body task that involves basic safety with dust control and a lathe.

@kablakeman has already done some work on this. So, if you would like to take this on, you should talk to him about it.
## Requirements
- Smooth to 0.001" surface roughness (ignoring micro-voids in the adhesive)
- Do not sand into the CF! (leave some patches unsanded, if necessary)
- Also do the nosecone

## Intended solution

Fix one end of the module on a dummy ring and attach a spider to the other end. Chuck the dummy ring in the lathe and use a _live_ center to hold the spider. Use sandpaper to grind down the surface. Use 320 grit to take off the "goosebumps," 800 to flatten it, and 1500 to finish.

For the radome, spray the surface with high-temp paint (_not_ matching the color of the radome) before sanding. Move to the 1500 when you get to the point where the paint only remains in the creases. This might be a good optional step for the CF modules too.

It may end up that the lathe won't work for this, in which case they will have to be sanded by hand. This process should be tested on the 18" CF module _before_ the radome or 24" modules, since the 18" CF is not mission-critical.
## Additional Safety

Talk to Alex Chally about appropriate safety measures. Don't put your hand on the rotating part (!!!), tension a piece of sandpaper instead. Use plenty of water to mitigate dust. Put down towels under the part. Wear a respirator for good measure.

Joedang, 2017-04-06:
## Update
The current plan is that @kablakeman will make some wood sections (below) that will bolt to the layup table.

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

These sections will connect to a spider via a threaded rod. So, we can set up a low-torque lathe-like thing (below).

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

#### Why this is a good idea
* We can have someone control the rate of rotation with one hand on the trigger of a drill while they control the pressure/position of an abrasive pad with the other hand (more control).
* This is probably less risky than doing it on a lathe.
* We don't need to worry about ruining any expensive equipment.
* We don't need any special room access to do this.

andrewgreenberg, 2017-04-06:
5/5 Andrews agree this is a very good idea, especially since we can use this for all the modules at our leisure.

kablakeman, 2017-04-16:
I uploaded a caveman-esque-CAD of the sanding module I am working on. Comments and criticisms appreciated. Sorry about the DWG. I'm a heathen.

Joedang, 2017-04-17:
I have a few comments.

* Do you have any other formats you can export to like STEP, IGES, or PDF? DWG is essentially unopenable without AutoCAD.
* I would make both ends of the holes flat, to make them easy to clamp with bolts.
* The [spider](https://github.com/psas/lv3.0-airframe/blob/master/cad/finCan/spider.pdf) uses a [3/8" threaded](https://www.fastenal.com/content/product_specifications/TROD.304.pdf) rod to attach to the motor. If you make the hole for the shaft 7/8", we can use a [1604 bearing](https://www.bearingworks.com/bearing-sizes/#1600-inch-series) on either end to hold the rod.
* What are you planning to use to make the ends? I'd assumed it would be wood. 3D printing or laser cutting might also work.
* Is there a reason for making the outer arch concentric with the hole?

Joedang, 2017-12-07:
# Yet Another Update On the Sanding Rig

### what didn't work
The threaded rod ended up being kind of sucky. Since there was some clearance between the rod and the inside of the bearings, it would walk along them as it spun. After a few seconds, the module would just rub against the sides of the rig. We couldn't fix things to the threaded rod easily, even when locking nuts against each other. (It probably would have been fine, if the nuts were opposing an axial load, but they were opposing circumferential loads.)

### changes made
We replaced the threaded rod and nuts with a keyed shaft. Collars on the shaft keep the rotating assembly and keys from jiggling out of place. A key at the end of the shaft is used to transfer torque from the drill.

### use procedure
A plastic curtain needs to be behind the rig when in use, since it sprays water/adhesive slurry in the radial direction. For the same reason, the operator should wear coveralls (preferably disposable), gloves, goggles, and a dust mask.

With one hand, control the drill. Spray the module with water (squirt/spray bottle). With the other hand, press the sandpaper to the module. Stand so that the spray hits your coveralls. Use both the drill trigger and sandpaper pressure to moderate the speed. Apply more water as necessary.

Sand with 320 grit paper until you read the carbon fiber (small patches of the surface will appear black instead of blue/green). Use a dry paper towel to wipe away the slurry when checking your progress.  Finish with a light pass of 800 grit.

Be sure to clean up any slurry that sprayed the surrounding area and dispose of the curtain, coveralls, gloves, towels, and sandpaper.

# Remaining LV3a Sanding Jobs
### critical path
- [ ] nosecone (hand-sand; don't use the rig)

### non-critical path
- [ ] radome module (sand with 800 grit, coat with contrasting paint, sand down to adhesive layer)
- [ ] 18" module
- [ ] 24" module

Joedang, 2018-01-20:
Everything except for the uncoated and "dragonscale" modules have been sanded. Since they aren't going to be used for L-13, I'm going to consider this done.

Closed 2018-01-20.

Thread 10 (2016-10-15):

We lost the LV3 assembly?

7deeptide, 2016-10-15:
LV3 SolidWorks assembly only includes the CubeCradel. @IanZabel Should we roll back the changes, or was this intended?

IanZabel, 2016-10-15:
That was intended, There are a couple things missing that are required for the whole assembly that I am working on. As it stands it would be a bunch of loose assemblies right now.

Closed 2016-10-15.

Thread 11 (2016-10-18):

Layup Experiments

Joedang, 2016-10-18:
There are a few unresolved/open questions surrounding the layup process. Individually, each is pretty simple, but they all require a cure cycle. The new oven may make this easier, if we're allowed to walk away from it.

* When laying up many layers of prepreg, do the layers slide around during curing? What's the porosity like? Can the prepreg be mixed with a 2-part epoxy?
* The new shrink tape doesn't really release from parts like the old shrink tape (supposedly it was the same product...). Are there any better methods for releasing the shrink tape other than using release film?
* If you replace the venturi pump with a mechanical pump, does that significantly increase compaction? (The hardest part of this is acquiring and setting up the pump.)
* How well would it work to layup CF into/onto a sharp corner if you cut sheets to butt up against the edge and just use many layers?

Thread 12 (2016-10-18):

Resurrecting the 2.3 Nose Mold

Joedang, 2016-10-18:
During its first layup, the latest nose mold partially adhered to the CF. When it cooled, the mold shrank around the CF and pulled itself apart. None of the portions that interface with aluminum parts are damaged, so it's possible we could epoxy it back together and use it again.

This will be a relatively straight forward layup, but require a 10 hour cure. Also, getting it in the oven without breaking it _while it's in the vacuum bag_ could be tricky. Since it won't fit in the new oven, I'll need at least one volunteer to do a shift of oven monitoring.

Joedang, 2017-04-06:
There's not much point in pursuing this when determined that the plug and low-temp materials work better.

Closed 2017-04-06.

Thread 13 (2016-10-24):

Phase Change Plate

Joedang, 2016-10-24:
## problem description

One concern for the fin can is the heat from the motor. The epoxy matrix in the carbon fiber shell can't go above 350 F. We don't really know how hot the motor gets though. The motor pushes up against the bottom of the rocket with an aluminum flange (see diagram). This is how the thrust of the motor actually gets transferred to the rocket. At the top of the motor, there's the spider ring, which keeps the motor from falling out of the rocket before and after firing. The spider is __*not*__ load-bearing.

The idea behind this phase change plate is to have a material with a melting point *below* 350 F between the thrust flanges. Thus, when the motor's thrust flange goes above that melting point, the temperature will level out, since heat will be going into the phase change of the plate rather than its temperature. This will buy us a little time before the epoxy matrix starts to overheat.

We can't simply make an annular disc of our phase change material (PCM) and stick it between the flanges. If we did that, the spider would become the load-bearing part as the PCM begins to melt. Neither the spider ring nor the holes it mounts to are designed to take the whole 9x the weight of the rocket and could break. So, there will need to be some additional structure to transfer the load between the flanges (perhaps concentric aluminum rings). We also don't want the PCM to leak out and catch fire (again, concentric aluminum rings might work).

## diagram
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

## requirements

#### must
* use a PCM that melts below 350 F
* continue to transfer the load through the thrust flanges after the PCM has completely melted, in a way that does not damage the thrust flange or the spider ring
* completely contain the PCM after melting so that it does not spill out or catch fire

#### should
* give some indication of the temperature the motor flange reached (color change paint? different PCM layers?)
* perform a test using a static load up to 400 F

## suggested action
(I'm going to add a suggested course of action... Hopefully I won't forget.)

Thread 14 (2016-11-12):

Thermal Sensing

Joedang, 2016-11-12:
# Thermal sensing for LV3.

### Description
The temperatures that the airframe will experience -- namely at the motor mount and the tip of the nose cone -- are a bit of an open question. It would be a good idea to have temperature measurements at these points, and perhaps a few other stations along the length of the rocket.

### Difficulty / Specializations
This would be a good project for a sophomore or junior MME and ECE to collaborate on. It involves data collection, calibration, simple circuit design, simple mechanical design, and collaboration with other projects to make sure you aren't interfering with them.

### Requirements

##### Must
* Not interfere with any other subsystems (!).
* Record temperatures up to 200 C (400 F).
* Record at a rate of 0.5 Hz or better.
* Record at a resolution of +/- 3 C or better.
* Compensate for the temperature of the board.
* Record the temperature of the thrust flange.
* Not interfere with the assembly/disassembly of the rocket.
* Not catch on fire.

##### Should
* Be able to record temps at 2 to 7 different points throughout the airframe (thrust flange and nose cone tip take priority).
* Record temperatures below whatever the typical temperature is at 8 km above Brother's Oregon.
* Record at a rate of 10 Hz or better.
* Record at a resolution of +/- 0.25 C or better.
* Use the same power, voltage, and data standards that the rest of the flight computer uses, in case we want to integrate it into another board at some point.
* Not add significant complexity to the assembly of the flight computer, recovery system (!), eNSR, or the rocket in general.
* Be easy and cheap to manufacture and test/calibrate.
* Be extensible to use other physical sensors. (This requires the ability to see the future.)
* Be applicable to thermal sensing on OreSat.
* Not shake apart when launched on a rocket.

### Suggested Action
There are a few ways to go about this, but I think the best right now would be to have a centralized thermal sensing board in the flight computer with cables running to thermocouples throughout the rocket.

In lower temperature applications, it would make a lot more sense to use a pre-fab thermistor, but those generally don't operate above 130 C (300 F). I'm concerned about whether or not the temperature is exceeding 177 C (350 F), which is the maximum working temperature of the epoxy matrix in the airframe.

On the electrical side of things, you *could* make high-input-impedance amplifiers for each thermocouple and do the cold-junction compensation and calibration on your own... or you could *not* re-invent the wheel and just use an existing IC to do it. (An initial internet search suggests the [MAX31855](http://datasheets.maximintegrated.com/en/ds/MAX31855.pdf) might be a good choice.) Either way, you have to be able to record the temperature data to and SD card. Whether or not you do this on the thermal sensing board or by sending the data to the flight computer is up to you and the other relevant ECE peeps. You will also need to make sure your design can handle any of the thermocouples being suddenly disconnected.

For the mechanical stuff, the big challenge is figuring out how you're going to pass the thermocouple wires between the modules. You will need something that can disconnect at each coupling ring. Most importantly, you will need something that can reliably disconnect at the eNSR without snagging and without interfering with the recovery system. I was thinking ethernet plugs would work well at the coupling rings. Perhaps the connection at the eNSR could have an ethernet plug with the tap cut off, so it simply pulls apart. Reusing the design from the umbilical disconnect may be a better option though, since it's a flight-tested design.

##### The electrical team member should:
* Look at possible ICs that could make this easier.
* Talk to people working on the flight computer to figure out whether you can share power, data, and/or board space with them.
* Figure out what your design constraints are. Where can you run cables in/out of the flight computer? Are you storing the data on the thermal sensing board or on the flight computer? Will you transmit the data to the ground station or just let it be retrieved from an SD card?

##### The mechanical team member should:
* Begin playing with different possible disconnects.
* Talk to people working on the flight computer, recovery (!), eNSR (!), RCS, and airframe to figure out what your design constraints are, so you don't break their projects and vice versa.
* Think about how you will calibrate each thermocouple once it is fixed in place on the rocket.

### Extended Background
Composites work by having lots of strong/rigid fibers gooped up in a flexible matrix. The matrix transfers stress between the fibers. And, because the fibers are very long compared to their width, the matrix has a lot of area with which to transfer this stress. So, the matrix only experiences a small fraction of the total stress and the whole material takes on the properties of the individual fibers.

If the matrix gets donked up though, it kind of ruins the whole thing. So, it would be bad if our matrix got too hot. It would start to chemically break down and become weaker. We definitely want to know if this is happening. (Plus, getting to experiment with heat transfer and trans/supersonic heating is awesome.)

A thermocouple is just two different metals welded together. The different metals have valence electrons with different energy levels. This essentially makes a waterfall of electrons from one metal to the other. The hotter this junctions gets, the more often electrons will wander into it. So, higher temperature means higher voltage. To form a circuit you need two such junctions (intermediate junctions just cancel), so if you know the voltage difference, you also need to know the temperature of one junction to know the temperature of the remaining junction. The junction you're measuring is usually referred to as the hot junction and your voltage measuring device is the cold junction (hence "cold junction compensation"). The junctions creates a constant voltage, but it's small (microvolts) and will saturate easily so you need a high gain low input impedance amplifier. Check out the Wikipedia pages on [the Thermoelectric Effect](https://en.wikipedia.org/wiki/Thermoelectric_effect) and [thermocouples](https://en.wikipedia.org/wiki/Thermocouple) if you want to know more.

kwilsonpdx, 2016-11-12:
* If the system controller board from OreSat is used for lv3.0 avionics, then this issue may be related:

https://github.com/oresat/system-controller/issues/10

Joedang, 2016-11-12:
Yeah, it sounds like we want to do the same thing. Do you know if anyone is currently working on that?

Have you guys thought about what connectors would be used on the board? I imagine the standard K-type connectors, for example, would be excessively large.

kwilsonpdx, 2016-11-13:
* The oresat issue referenced is a proposal for the next system controller board revision.
* Connector type(s) will depend on sensor type(s) (RTD or Thermocouple) and use case (flight or prototype). We should have more insight after we capture the requirements for the next revision.

Joedang, 2017-04-12:
# Update
After talking with @andrewgreenberg and Kenny, it seems best to have a simple/hacky solution for L-13. Once we are trying to use OreSat as our flight computer, then we can worry about more complicated solutions.

Basically, the sensor should be a small Arduino-compatible board with some off-the-shelf thermocouple and/or thermistor, a LiPo battery that will last at least 6 hours, and an SD card to store its data. The sensors will just be attached to the aluminum bits using thermal epoxy.

Ideally, it should also have some way of identifying when launch occurs to within 1 second. Ideally, it should append the data to the SD card every second, in case the battery shakes loose.

Whoever puts this together, it's your choice on whether you want to have one board per location or run wires along the length of the rocket. If you go with the latter option, it needs to be very thin wire with lots of slack (~2 ft) near the eNSR, so it will just tear away when the nosecone separates.

RocketmanYG, 2018-04-07:
Thermal sensing for LV3 is done! We can now store temperature data to an SD card and see how hot LV3 carbon fiber airframe is going to get.

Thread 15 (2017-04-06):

How do the Radial Mounting Holes for the Cubesat Cradle Lid Work?

Joedang, 2017-04-06:
So, I was touching up the technical drawing for the cradle lid ([part][lid part], [drawing][lid drawing]), moving dimensions out of the part profile, consolidating views, et cetera. I noticed that the mounting holes on the side ("6X DIA .1200 THRU") are a different size than what's on ~~the [motor mount] (# 4-40 Helicoil) or~~ the [spider] (0.129" diameter). What's the plan with those? are they going to have nuts on the other side?

[lid drawing]: https://github.com/psas/lv3.0-airframe/blob/master/cad/CubeSatAirframeMount/CradleInterface_TechDrawing.pdf
[lid part]: https://github.com/psas/lv3.0-airframe/blob/master/cad/CubeSatAirframeMount/Cradle_lid_attachment_II.SLDPRT
[motor mount]: https://github.com/psas/lv3.0-airframe/blob/master/cad/finCan/motorMount.pdf
[spider]: https://github.com/psas/lv3.0-airframe/blob/master/cad/finCan/spider.pdf

IanZabel, 2017-04-06:
I used the same dimensions as the [ring holes](https://github.com/psas/lv3.0-airframe/blob/master/cad/module/femaleRing.SLDPRT), are they threaded in the female/male module rings? My original intention was to bolt from the [cradle lids](https://github.com/psas/lv3.0-airframe/blob/master/cad/CubeSatAirframeMount/Cradle_lid_attachment_II_V2.SLDPRT) to the module rings to make removing/inserting the cradle slightly easier.

Joedang, 2017-04-06:
The mounting holes on the inside of the female rings are normally threaded, yeah. (Not the holes for male + female but the ones for female + spider.)

On second thought, the way you have it makes a lot of sense. The holes on the spider aren't tapped because it's the head of the screw that provides the clamping force. It might be a good idea, though, to use some plastic washers when we're mounting it since that inside surface isn't flat.

jalouke, 2017-04-07:
I just want to make sure that I am not missing something. Unless the LV3 rings have changed, the Male rings are threaded, and the female rings have a non-threaded hole

Joedang, 2017-04-08:
The rings have not changed. I can't get to SolidWorks until Monday, but here's more or less how it works. The male ring has one threaded hole. The female has two holes (heh): one plain countersunk hole that attaches it to the male ring and one threaded hole on the inside that attaches it to whatever payload.
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

jalouke, 2017-04-08:
I forgot about those holes. However the spider actually attaches to the male ring (the threads are deep enough to have a screw inserted from both sides.

hmarie2, 2017-04-08:
Hey guys, this seems like a conversation that is more appropriate for
Basecamp so it doesn't clutter up people's inboxes. Joe, maybe you can get
the guys added and start a new project or team?

Thanks,

Marie

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
--
Marie

Joedang, 2017-04-09:
> the spider actually attaches to the male ring (the threads are deep enough to have a screw inserted from both sides.

Huh, I never considered that, but yeah, that makes sense.

> this seems like a conversation that is more appropriate for
Basecamp so it doesn't clutter up people's inboxes.

Sorry for the clutter. I think it's more appropriate on GitHub than Basecamp though, since it's about a part and not people/logistics. I'd suggest unsubscribing from the issue or unwatching the repo if it's a problem.

Joedang, 2017-05-21:
Reason for closing: original question seems to have been answered.

Closed 2017-05-21.

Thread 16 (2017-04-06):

Sled Jig Machining

Joedang, 2017-04-06:
The sled jig ([drawing], [part]) aligns the rail sled  (issue #7) on the [fin can][assembly] and on the RCS module. It's probably the most straightforward part in the airframe yet, since everything is planes and holes at right angles with some chamfers and countersinks. The CAD is all done and we probably have suitable stock in the rocket closet. Someone just needs to make it. Perhaps @JacobTiller or @SaturnVF1?

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

[drawing]: https://github.com/psas/lv3.0-airframe/blob/master/cad/railSled/sledJig.pdf
[part]: https://github.com/psas/lv3.0-airframe/blob/master/cad/railSled/sledJig.SLDPRT
[assembly]: https://github.com/psas/lv3.0-airframe/blob/master/cad/finCan/finCanLayup.SLDASM

SaturnVF1, 2017-04-06:
Is it aluminum? If Jake doesn't have a chance to use a real shop I could probably do it in the LID.

Joedang, 2017-04-06:
Yup, it's aluminum. The giant "LV3" blocks are probably big enough, but cutting off a piece might be obnoxious.

Joedang, 2017-05-21:
Reason for closing: @SaturnVF1 made the thing.

Closed 2017-05-21.

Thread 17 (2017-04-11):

Fasteners for CAD Models

Joedang, 2017-04-11:
# The Problem
Most/all of the CAD for LV3 does not include fasteners, even though we have particular ones in mind.

# The solution
- [ ] Go through and identify all the fasteners. I'm pretty sure it's just:
  - [ ] countersunk screw (hex) for connecting modules
  - [ ] machine screw (hex) for mounting internals to modules
_Note: make sure the countersunk and machine screws won't collide when attaching the spider! They enter the same hole from opposite ends. ([see example drawing](https://github.com/psas/lv3.0-airframe/blob/master/cad/couplingExample.pdf))_
  - [ ] optional (plastic) washer for internals
  - [ ] threaded rod for connecting motor to spider
  - [ ] nut for attaching motor to spider
  - [ ] threaded rod for attaching nose tip to nose plug
- [ ] If necessary add callouts to the relevant model/drawing for the fasteners.
- [ ] Find SolidWorks models for all the fasteners and put them in `cad/COTS`.
- [ ] Add the fasteners to the assemblies.
_Mate countersunk screws as coincident cones and everything else as concentric holes with contacting faces._
- [ ] Update the drawings, superassemblies, and PDFs.

Joedang, 2017-07-01:
@RocketmanYG, you said you wanted to make a BoM for LV3. This would be some relevant stuff for that.

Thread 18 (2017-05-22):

Missing Fillet in Spider Drawing

Joedang, 2017-05-22:
The fillet between the arms and feet, if you will, of the spider isn't called out in [this drawing.](https://github.com/psas/lv3.0-airframe/blob/master/cad/finCan/spider.pdf) (Most obvious in the 3D view on sheet 1 and in section C.) Someone (probably me, next time I'm on SolidWorks) should add that.

IanZabel, 2017-05-22:
I added the callout to the leg-feet fillet (section D) on sheet 3 just below the existing section C view. Let me know if you want any changes made and cant make it to Solidworks anytime soon.

Closed 2017-05-22.

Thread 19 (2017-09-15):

LV3 Spec Sheet

Joedang, 2017-09-15:
We should totally collate specification sheets for the flight hardware of LV3. Example data we would want to include:
* Component level
  * Mass
  * CoM
  * Failure load for various modes
  * Maximum working temperature
  * Fastener sizes
  * Failure acceleration (obviously not meaningful for parts that support other parts)
* System level (include expected/flown data)
  * Acceleration
  * Altitude
  * Air speed / Mach number
  * Times flown
  * Mass / weight

Joedang, 2018-03-07:
This is sort of a thing [here](https://github.com/psas/lv3.0-airframe/blob/master/doc/quickFacts.md).

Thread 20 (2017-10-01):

Achieving suborbital with solids.

rgregoryclark, 2017-10-01:
Amateur groups have sent flights to the Karman line of 100 km for suborbital space, but no university team has accomplished it yet. It might be doable by liqhtweighting the casings used on your solid motor  launch vehicles by replacing the aluminum with carbon fiber.

 I saw on your web pages you have used carbon fiber airframes. But what's more than that that needs to be done is replace the actual casing on the motors with carbon fiber. For example, the N-class solid motor used on your LV 2.2, you could have it delivered from the manufacturer with the propellant in just its sleeve and you would make the casing for it in carbon fiber.

 If the one N-class motor with carbon fiber casing does not reach suborbital space, you almost certainly would be able to reach it in two stages. The second stage again would replace the aluminum casing with carbon fiber.

  Bob Clark

andrewgreenberg, 2017-10-01:
Hi Bob! See my response to your email on the PSAS list. I'm closing this issue.

Closed 2017-10-01.

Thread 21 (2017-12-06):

Mass Measurements

Joedang, 2017-12-06:
We need to know the magnitude and location of the center of mass of all the rocket components. Once measured, these values must be added to [the OpenRocket model](https://github.com/psas/lv3.0-airframe/blob/master/sim/ORK/LV3_L13a_ideal.ork).

- nosecone with tip
  - [ ] measurement
  - [ ] OR model
- recovery system
  - [ ] measurement
  - [ ] OR model
- 18" module
  - [ ] measurement
  - [ ] OR model
- 24" module
  - [ ] measurement
  - [ ] OR model
- fin can
  - [ ] measurement
  - [ ] OR model
- spider
  - [ ] measurement
  - [ ] OR model
- cradle mount
  - [ ] measurement
  - [ ] OR model
- cradle frame
  - [ ] measurement
  - [ ] OR model
- cradle spacers
  - [ ] measurement
  - [ ] OR model
- engine casing
  - [ ] measurement
  - [ ] OR model
- engine core
  - [ ] measurement
  - [ ] OR model
- thrust flange ("motor mount", "pizza", etc.)
  - [ ] measurement
  - [ ] OR model
- camera module
  - [ ] measurement
  - [ ] OR model
- umbilical module
  - [ ] measurement
  - [ ] OR model
- telemetrum
  - [ ] measurement
  - [ ] OR model
- RCS (any CoM estimate is vapor for now...)
  - [ ] measurement
  - [ ] OR model

Joedang, 2018-01-20:
## Update: Took Physical Measurements
Rather than put everything here, I put my measurements [in this file](https://github.com/psas/lv3.0-airframe/blob/master/test/massMeasurements.md). (See the file for more info.)

Joedang, 2018-05-09:
Hey @jejor, you should go measure the things. You'll need to get a recovery person to get the parachutes out for you... someone like @hmarie2 or @calvin-young.

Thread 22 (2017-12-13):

The Cubesat Cradle Doesn't Fit in a Single Module

Joedang, 2017-12-13:
See the note in #21 .

Internal flight hardware is only supposed to mount to the male mounting holes of the furthest upstream module it occupies and the female mounting holes of the furthest downstream module it occupies. (i.e., you can't steal the mounting holes of the module next to you.)

The cradle will need to be modified to fit inside a single module before we fly the RCS, since it's currently stealing the female mounting holes of the RCS's module. (Fortunately, we aren't flying the RCS on L-13.)

There are a couple of spacer plates we can take out to shorten the assembly, but the "cradle interface ring" may need to be shortened as well.

(This reminds me, we should have a contribution guide for LV3.)

Joedang, 2018-07-17:
This was fixed with commit 87c7b8f.

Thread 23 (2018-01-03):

Umbilical + switch ring

Joedang, 2018-01-03:
## Problem
We are legally required to have some way to enable/disable the launchy bits after the rocket's assembled. Also, after L-13, we will probably want to be able to provide power and data up until the launch.

## Suggested Solution
Create a ring with the usual M/F interfaces with holes for switches and a power/data umbilical connection.

JSRoland, 2018-01-04:
Hey Joe,
There is a repo for this project here: https://github.com/psas/sw-cad-airframe-umbilical-disconnect

Joedang, 2018-01-04:
Oh yeah, that's why it seemed so familiar... :upside_down_face:

Closed 2018-01-04.

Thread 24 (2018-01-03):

Side-hole drilling jig

Joedang, 2018-01-03:
## Problem
We need to make radial holes is pretty much all our parts. The normal way to do this, sans 5-axis mill, is to use a rotary table. The down side is we don't have convenient access to one and they're not super repeatable.

 ## Suggested Solution
Create a set of jigs that interface with the easy-to-machine features of the rings/mounting parts.
This is already started in [module/jigs/](https://github.com/psas/lv3.0-airframe/tree/master/cad/module/jigs).

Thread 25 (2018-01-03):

Camera ring

Joedang, 2018-01-03:
## Problem
Since LV3 *is* a test platform for LV4 technology, it would be kind of nice to know if/how things go wrong. Right now, we only have acceleration and height from the Telemetrum, and will hopefully have temperature at the nose/tail.

## Suggested Solution
Stick some cameras on it.

Specifically, make an aluminum ring with M/F interfaces that will give us a $2\pi$ view of the nose and tail

### Requirements
- Survive 15 g acceleration
- Survive Mach 2 wind
- Survive a failed main chute deployment
- Able to sit at the launch tower for 2 hours (?) and still have enough power/storage to record the launch
- Loss of any/all cameras or connectors does not result in a significant loss of data (more of a CS requirement)
__i.e., when we run out of power after landing, all the data isn't lost__

Joedang, 2018-03-07:
This lives in [its own repo](https://github.com/psas/lv3.0-camera-ring) now.

Closed 2018-03-07.

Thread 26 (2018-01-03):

Order motor

Joedang, 2018-01-03:
## Problem
We don't have the flamey bit that makes us go to space.

## Suggested Solution
Get a Cesaroni 21062-O3400-IM.

andrewgreenberg, 2018-02-07:
Nope! Won't fit in our current motor casing, and it's not worth it to upgrade to a 6XL casing on our first flight. So we bought another CTI N2501. Perhaps this summer's flight we'll upgrade?

Closed 2018-02-07.

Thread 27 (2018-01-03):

Finish the cradle mounting rings

Joedang, 2018-01-03:
## Problem
The ring(s) that hold the flight computer in place aren't done. One is all done except for the radial holes, the other is hiding inside a plate of aluminum.

## Remarks
The top ring/plate/mount/whatever only retains the flight computer in place. Only the bottom ring bears the weight of the flight computer from launch, cute deployment, and landing. We can probably get away with using a 3D printed top ring or a designed-down ring.

## Suggested solution
Finish the radial side holes in the existing ring. (The current "best" option for this is probably to finish the side hole jig. See #24.)

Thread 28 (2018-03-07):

Make a Pretty Diagram of LV3 and its Subsystems

Joedang, 2018-03-07:
It would be nice to have [something like this.](https://github.com/psas/psas.github.com/blob/master/images/launch_12.png) We need/want a thing that will fit on a flier and give people an idea of what's on the rocket. I started a [quick facts sheet](https://github.com/psas/lv3.0-airframe/blob/master/doc/quickFacts.md),  which might be a nice thing to put alongside the diagram. You can get a to-scale outline of the rocket and subsystems from [OpenRocket](https://github.com/psas/lv3.0-airframe/blob/master/sim/ORK/LV3_L13.ork) or [SolidWorks](https://github.com/psas/lv3.0-airframe/blob/master/cad/LV3.SLDASM). Ask me, if you don't know how to do this. (As of right now, those models are missing the camera/umbilical rings.)

Joedang, 2018-07-17:
[That's here.](https://github.com/psas/lv3.0-airframe/blob/master/doc/L-13.1diagram.svg)

Closed 2018-07-17.

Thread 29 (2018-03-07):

Replace the Cradle Ring with the Camera Bulkhead

Joedang, 2018-03-07:
The bulkhead from [the camera ring](https://github.com/psas/lv3.0-camera-ring), although requiring more parts, is _way easier_ to manufacture than the current cradle ring. (The cradle ring requires a 2.5 axis mill and a rotary table, while the bulkhead only requires a 2.5 axis mill.) We should replace the cradle rings with a pair of bulkheads.

While you're (I'm?) at it, the length of the cradle cage will need to be changed, since the bulkheads sit at a different height from the mating surfaces of the module. Also, the acrylic plates that the rails sit on should be replaced with plywood. (Aaand there should be a drawing indicating the major grain direction of the cradle cage pieces. That should be its own issue, but bleh.)

Joedang, 2018-07-17:
Done. See 87c7b8f.

Closed 2018-07-17.

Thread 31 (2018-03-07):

Update the Fin Can Layup Procedure

Joedang, 2018-03-07:
[This document describing the fin can layup](https://github.com/psas/lv3.0-airframe/blob/master/doc/mfg/finProcedure.md) currently only reflects the "fin can of shame". The fin layup is pretty much the same, but needs to be updated with pictures. The stuff about bonding the fins to the module needs to be completely replaced with the jig/flange procedure.

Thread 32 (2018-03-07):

Perform EM Testing with the Assembled Flight Computer Module

Joedang, 2018-03-07:
It's probably a good idea to check how the module, cradle, and OreSat structure effect the radiation pattern of antennas stuck to the side of the cradle cage. Technically #29 will change the geometry a little bit, but it's probably a fine approximation to use the cradle ring. Actually, covering the ends of the module in foil might even be fine, since the bulkheads only have holes that are 1/8" diameter.

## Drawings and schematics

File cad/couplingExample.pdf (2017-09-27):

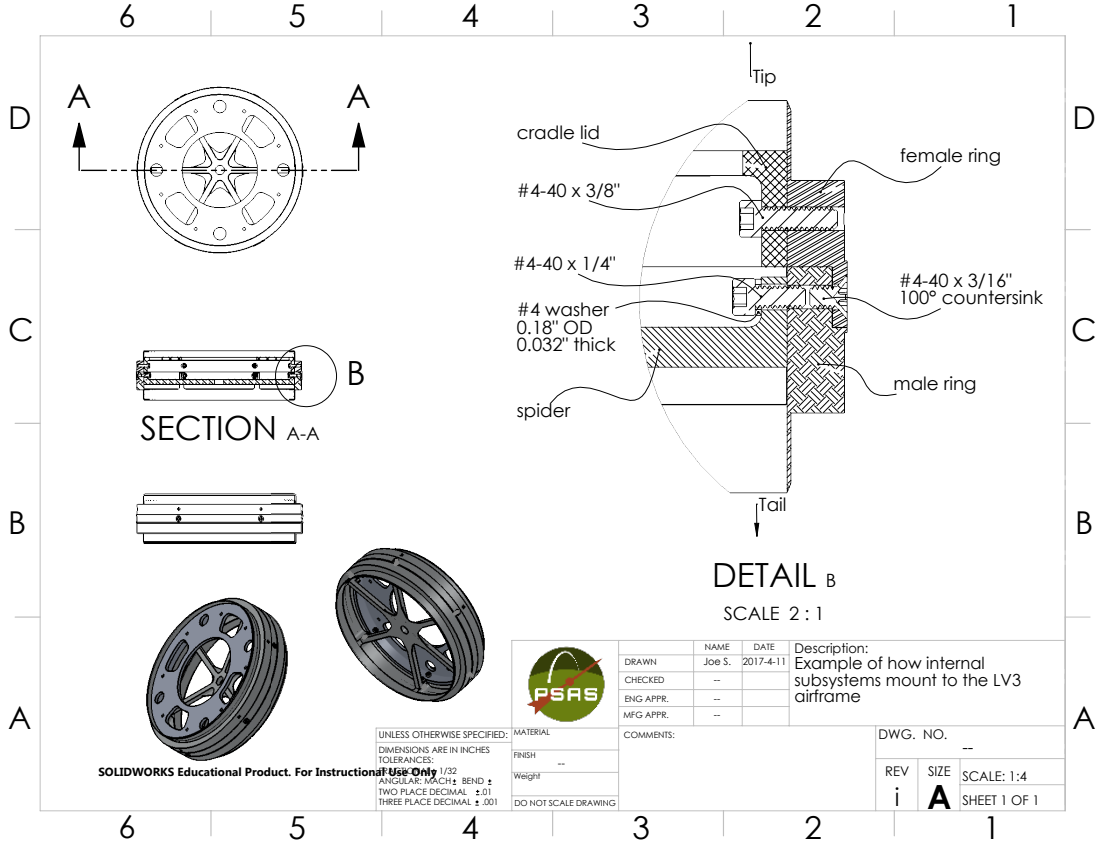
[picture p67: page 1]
SECTION A-A; DETAIL B; SCALE 2 : 1; male ring; female ring; cradle lid; #4-40 x 3/16" 100° countersink; #4 washer 0.18" OD 0.032" thick; REV; SCALE: 1:4; DO NOT SCALE DRAWING; SHEET 1 OF 1

NAME | DATE | Description: Example of how internal subsystems mount to the LV3 airframe

DRAWN | Joe S. | 2017-4-11
CHECKED | --
ENG APPR. | --
MFG APPR. | --

UNLESS OTHERWISE SPECIFIED: | MATERIAL | COMMENTS: | DWG. NO. --

DIMENSIONS ARE IN INCHES
TOLERANCES:
FRACTIONAL 1/32
ANGULAR: MACH BEND
TWO PLACE DECIMAL .01
THREE PLACE DECIMAL .001

SOLIDWORKS Educational Product. For Instructional Use Only

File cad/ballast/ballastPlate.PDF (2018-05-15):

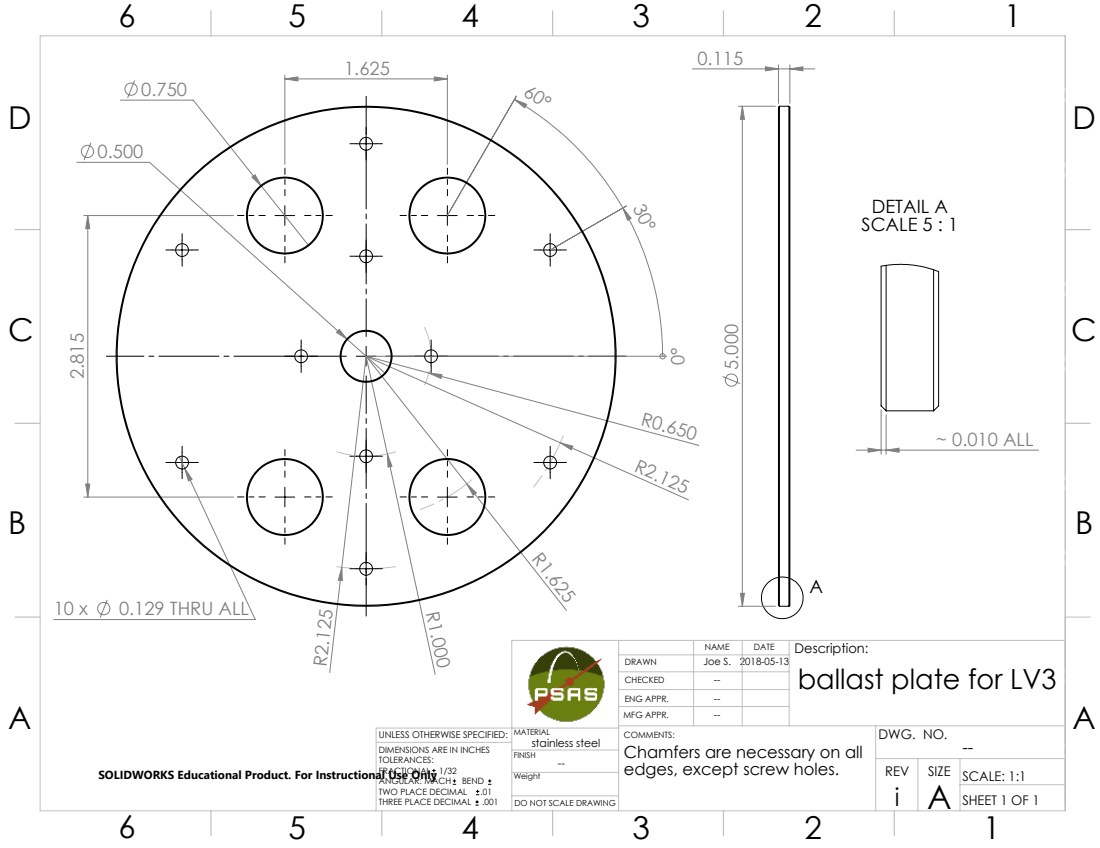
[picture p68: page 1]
0.129 THRU ALL; ~ 0.010 ALL; DETAIL A SCALE 5 : 1; REV; SCALE: 1:1; DO NOT SCALE DRAWING; SHEET 1 OF 1

NAME | DATE | Description: ballast plate for LV3

DRAWN | Joe S. | 2018-05-13
CHECKED | --
ENG APPR. | --
MFG APPR. | --

UNLESS OTHERWISE SPECIFIED: | MATERIAL stainless steel | COMMENTS: Chamfers are necessary on all | DWG. NO. --

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

edges, except screw holes. SOLIDWORKS Educational Product. For Instructional Use Only

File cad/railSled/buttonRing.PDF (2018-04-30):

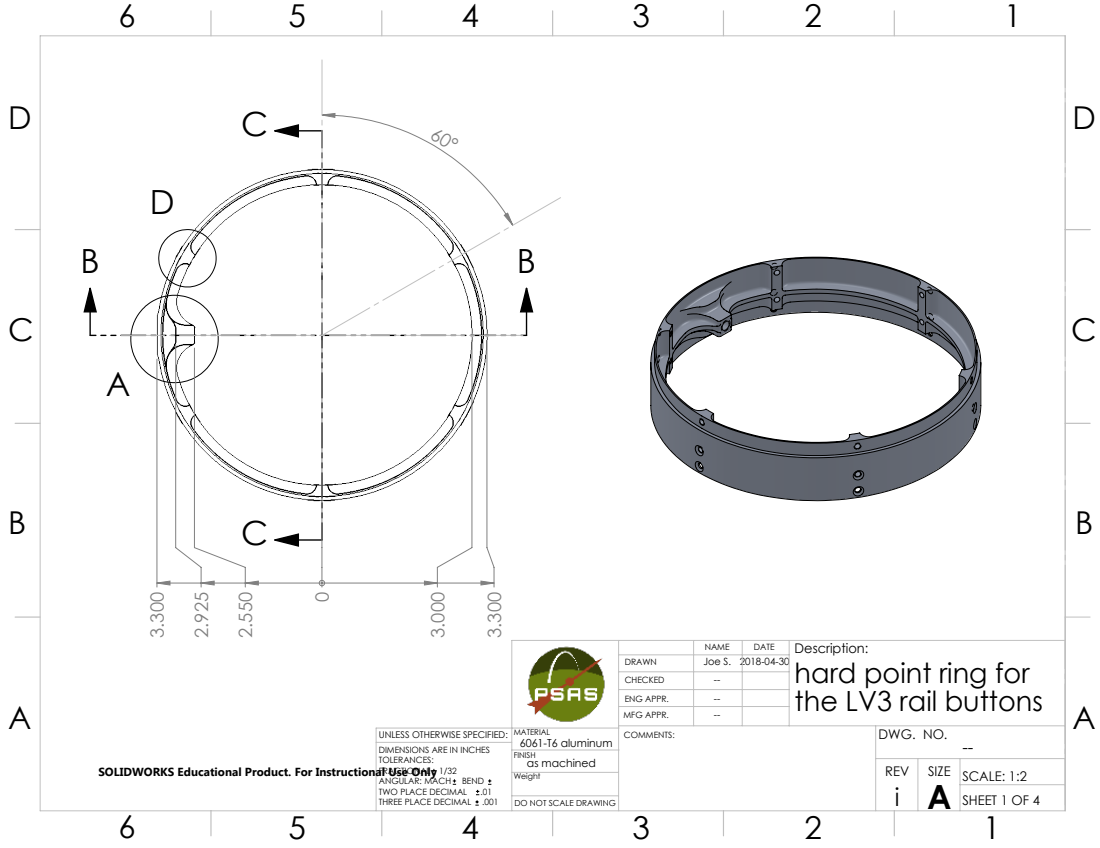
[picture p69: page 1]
as machined; REV; SCALE: 1:2; DO NOT SCALE DRAWING; SHEET 1 OF 4

NAME | DATE | Description: hard point ring for the LV3 rail buttons

DRAWN | Joe S. | 2018-04-30
CHECKED | --
ENG APPR. | --
MFG APPR. | --

UNLESS OTHERWISE SPECIFIED: | MATERIAL 6061-T6 aluminum | COMMENTS: | DWG. NO. --

DIMENSIONS ARE IN INCHES
TOLERANCES:
FRACTIONAL 1/32
ANGULAR: MACH BEND
TWO PLACE DECIMAL .01
THREE PLACE DECIMAL .001

SOLIDWORKS Educational Product. For Instructional Use Only

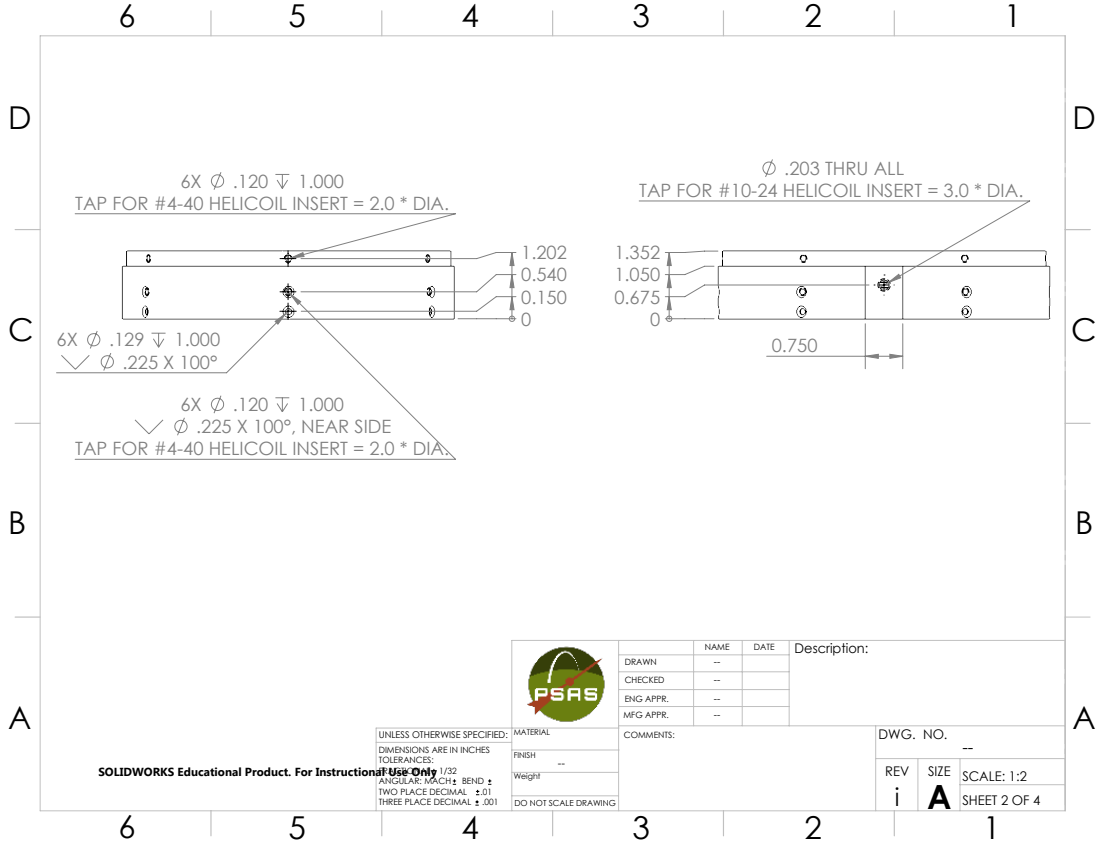
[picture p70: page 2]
.203 THRU ALL; .225 X 100°, NEAR SIDE; REV; SCALE: 1:2

TAP FOR #10-24 HELICOIL INSERT = 3.0 * DIA.

TAP FOR #4-40 HELICOIL INSERT = 2.0 * DIA.

NAME | DATE | Description:

DRAWN | --
CHECKED | --
ENG APPR. | --
MFG APPR. | --

UNLESS OTHERWISE SPECIFIED: | MATERIAL | COMMENTS: | DWG. NO. --

DIMENSIONS ARE IN INCHES
TOLERANCES:
FRACTIONAL 1/32

SOLIDWORKS Educational Product. For Instructional Use Only

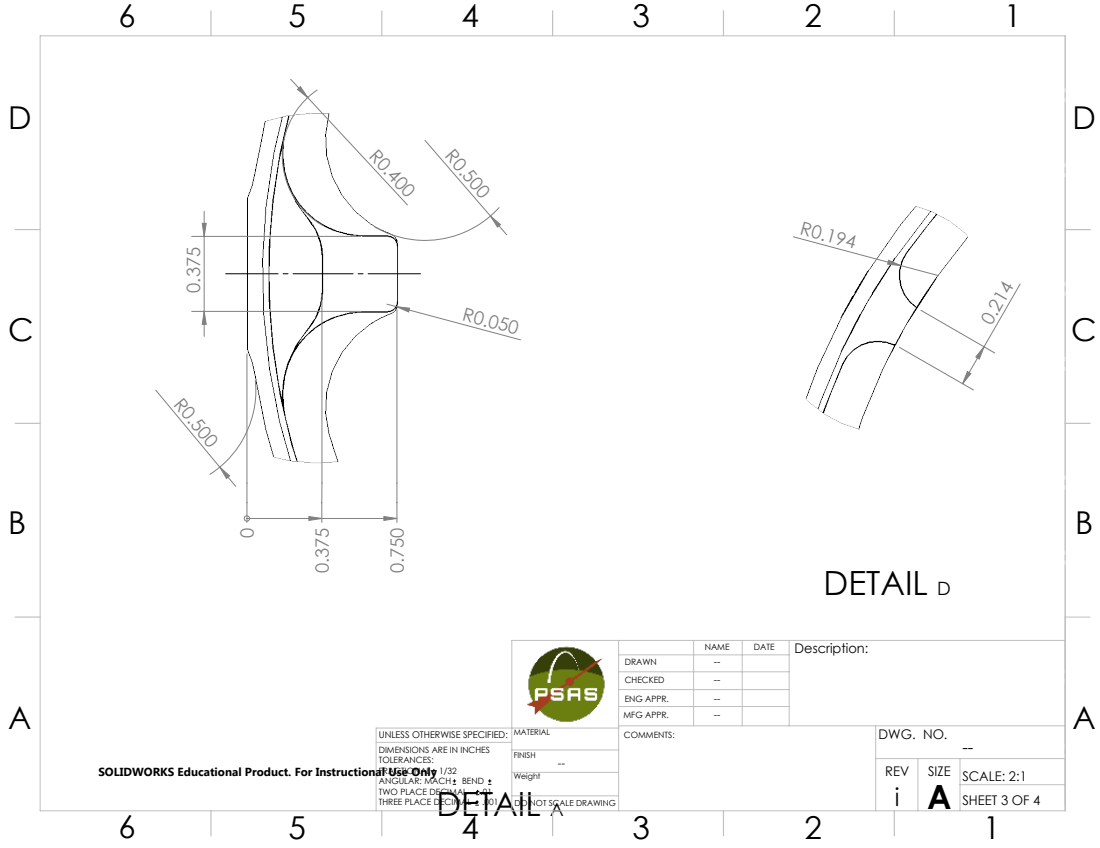
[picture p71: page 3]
DETAIL D; REV; SCALE: 2:1

NAME | DATE | Description:

DRAWN | --
CHECKED | --
ENG APPR. | --
MFG APPR. | --

UNLESS OTHERWISE SPECIFIED: | MATERIAL | COMMENTS: | DWG. NO. --

DIMENSIONS ARE IN INCHES
TOLERANCES:
FRACTIONAL 1/32
DETAIL A

SOLIDWORKS Educational Product. For Instructional Use Only

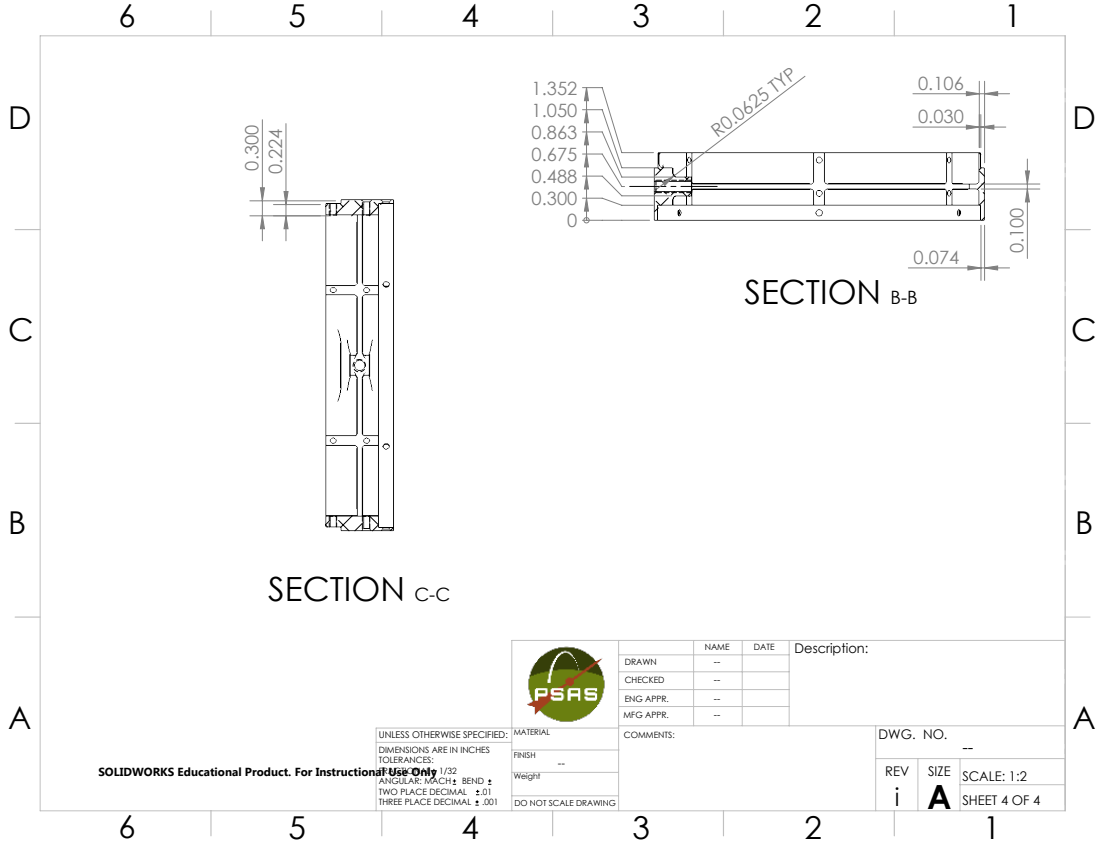
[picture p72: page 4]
R0.0625 TYP; SECTION B-B; SECTION C-C; REV; SCALE: 1:2

NAME | DATE | Description:

DRAWN | --
CHECKED | --
ENG APPR. | --
MFG APPR. | --

UNLESS OTHERWISE SPECIFIED: | MATERIAL | COMMENTS: | DWG. NO. --

DIMENSIONS ARE IN INCHES
TOLERANCES:
FRACTIONAL 1/32

SOLIDWORKS Educational Product. For Instructional Use Only

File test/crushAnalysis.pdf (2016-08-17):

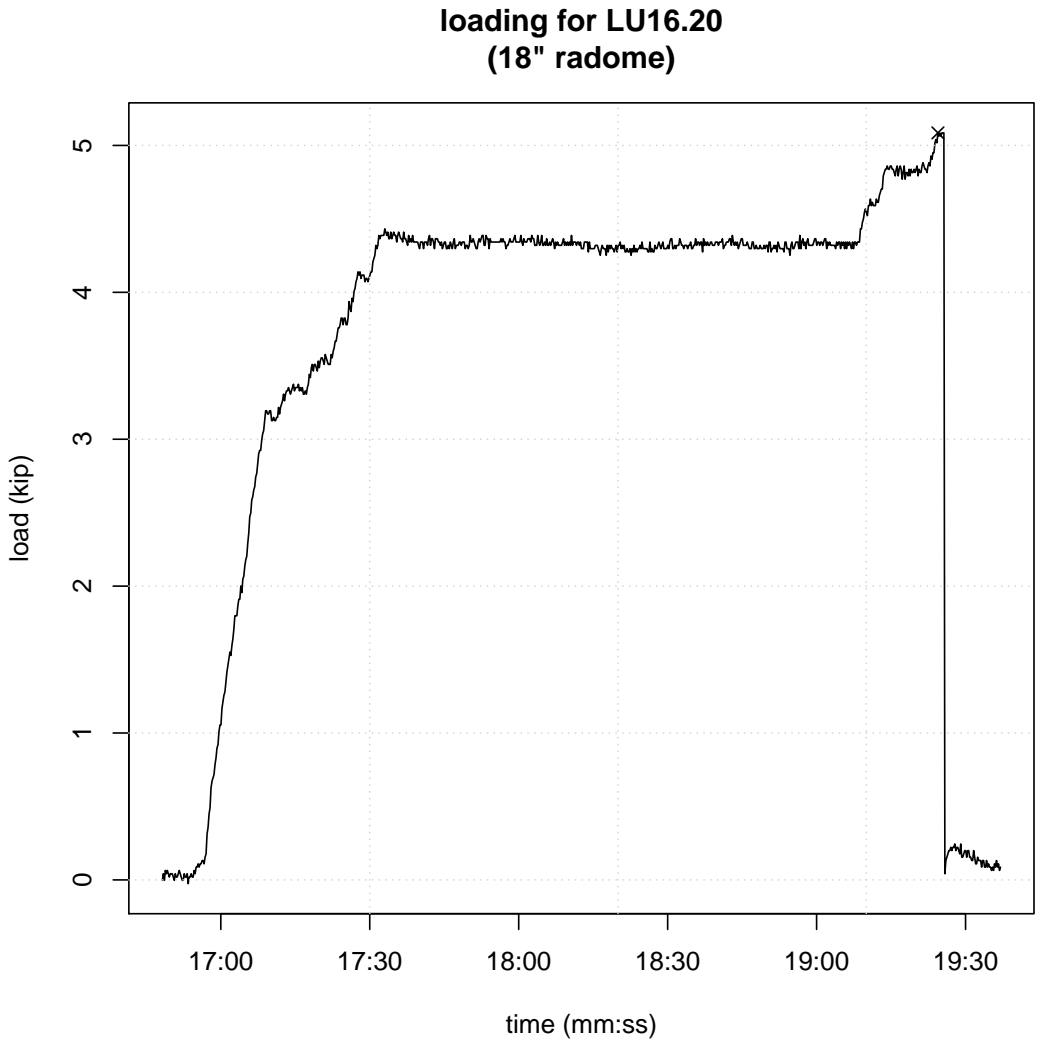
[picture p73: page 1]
loading for LU16.20 (18" radome); load (kip)

time (mm:ss)

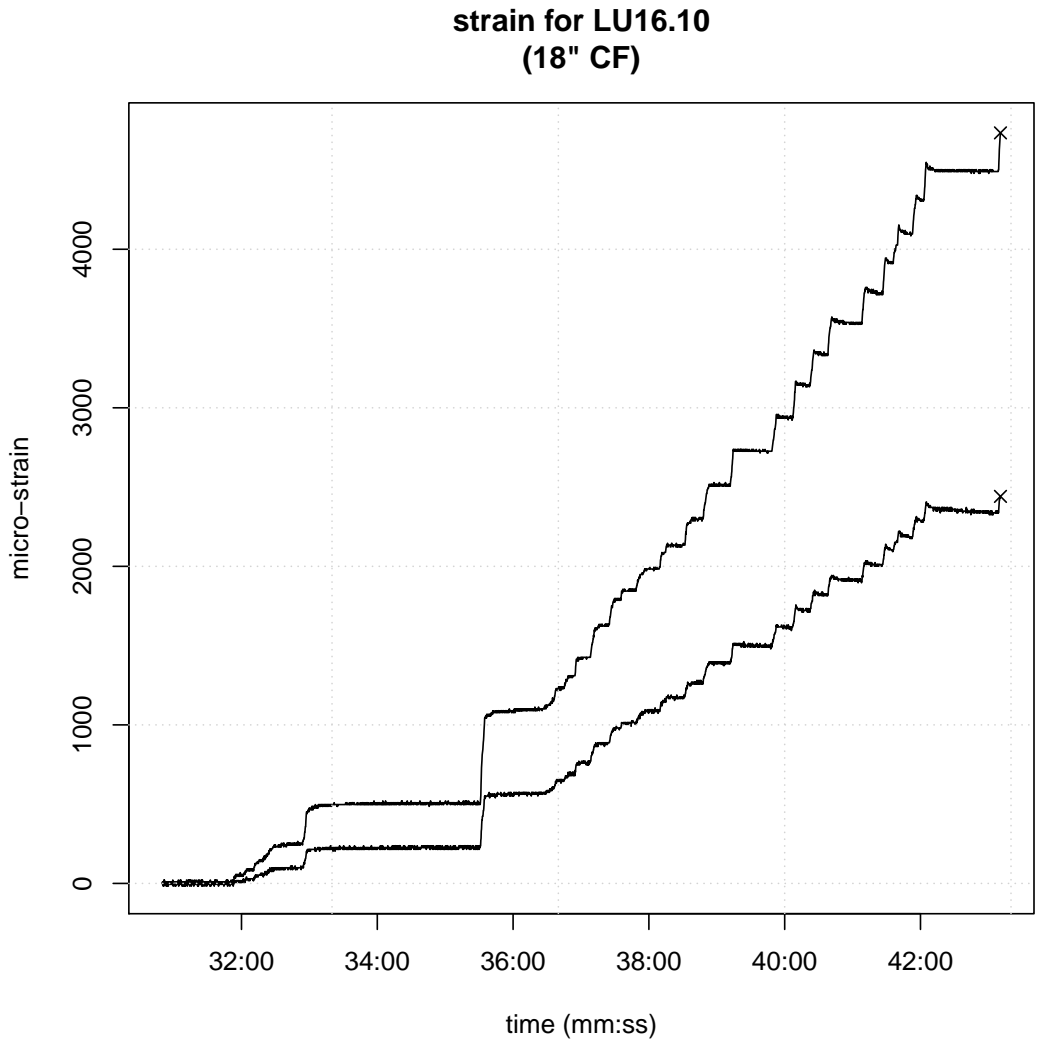
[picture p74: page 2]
strain for LU16.10 (18" CF); micro−strain

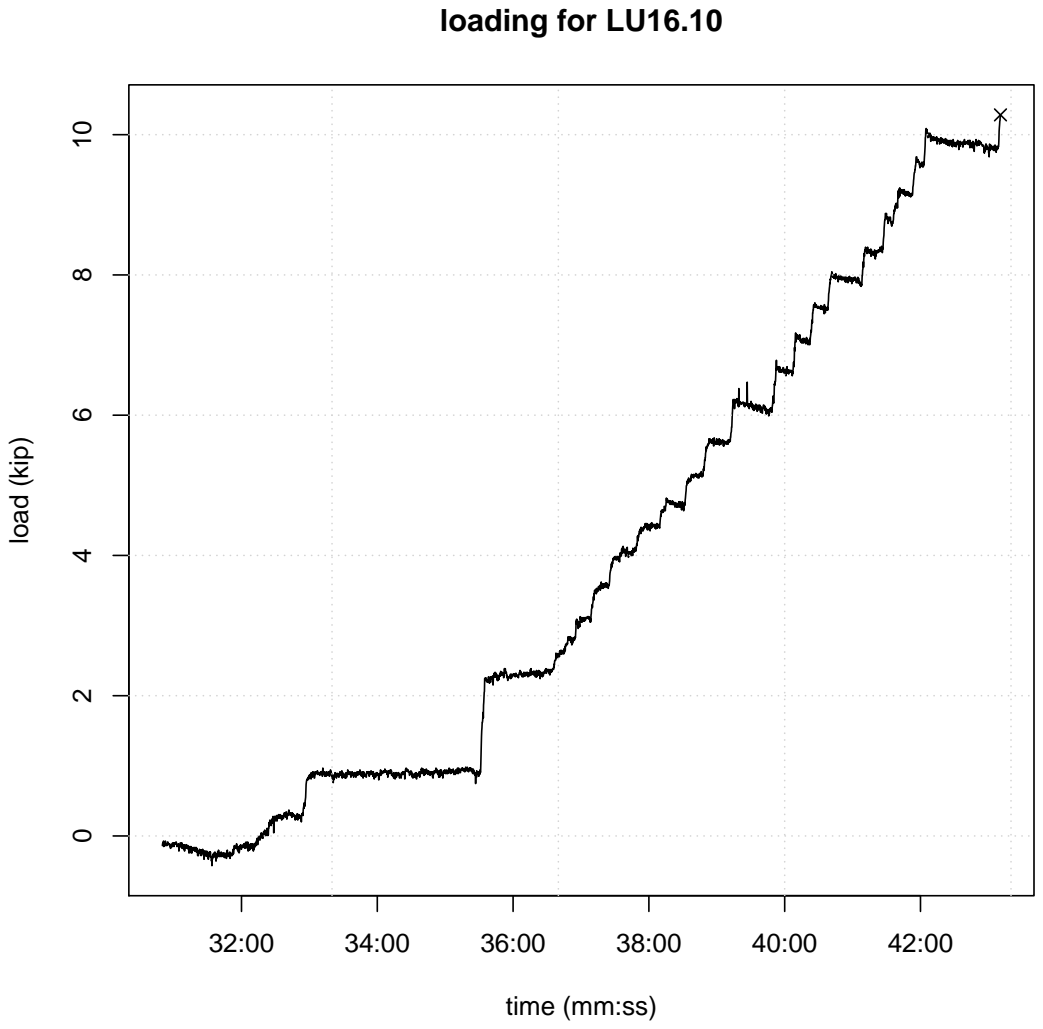
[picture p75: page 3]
loading for LU16.10; load (kip)

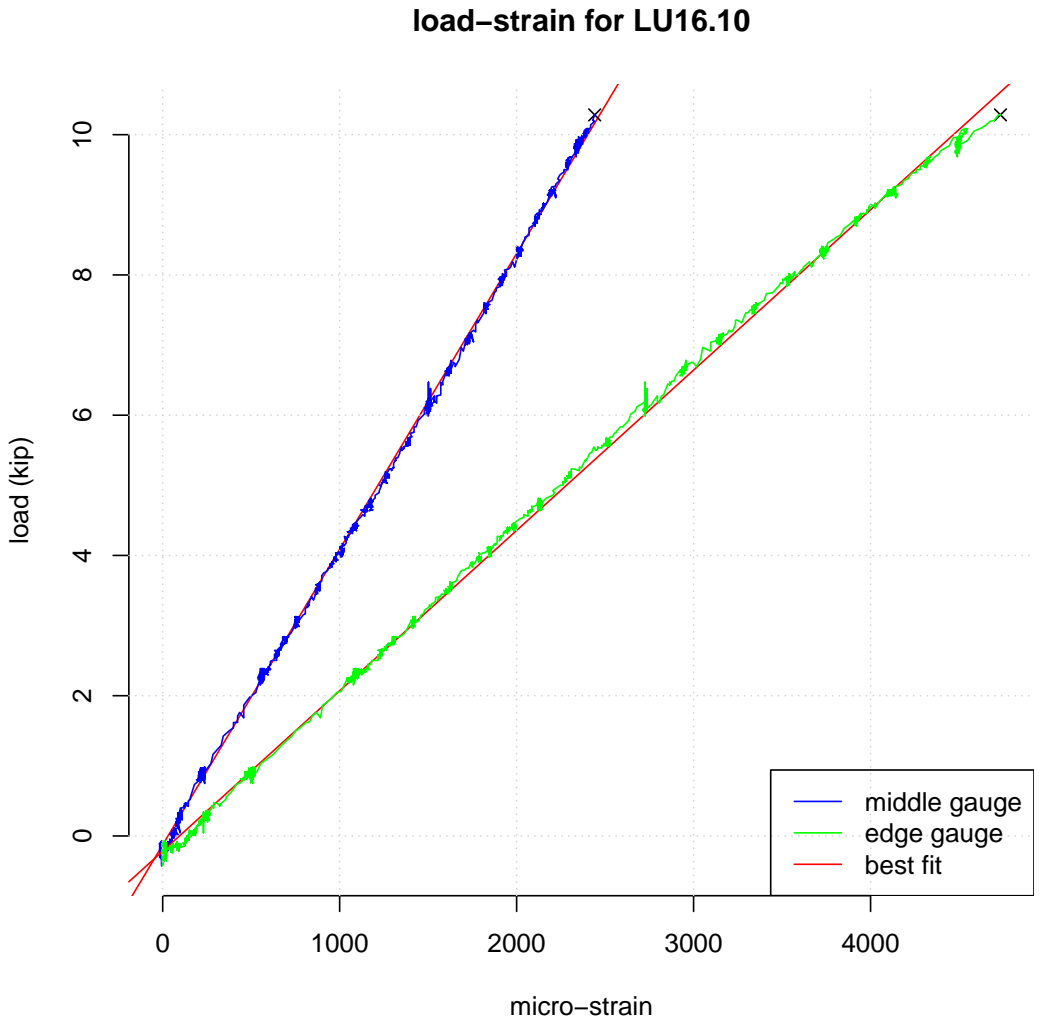
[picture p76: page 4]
micro−strain; load (kip); middle gauge edge gauge best fit

load−strain for LU16.10

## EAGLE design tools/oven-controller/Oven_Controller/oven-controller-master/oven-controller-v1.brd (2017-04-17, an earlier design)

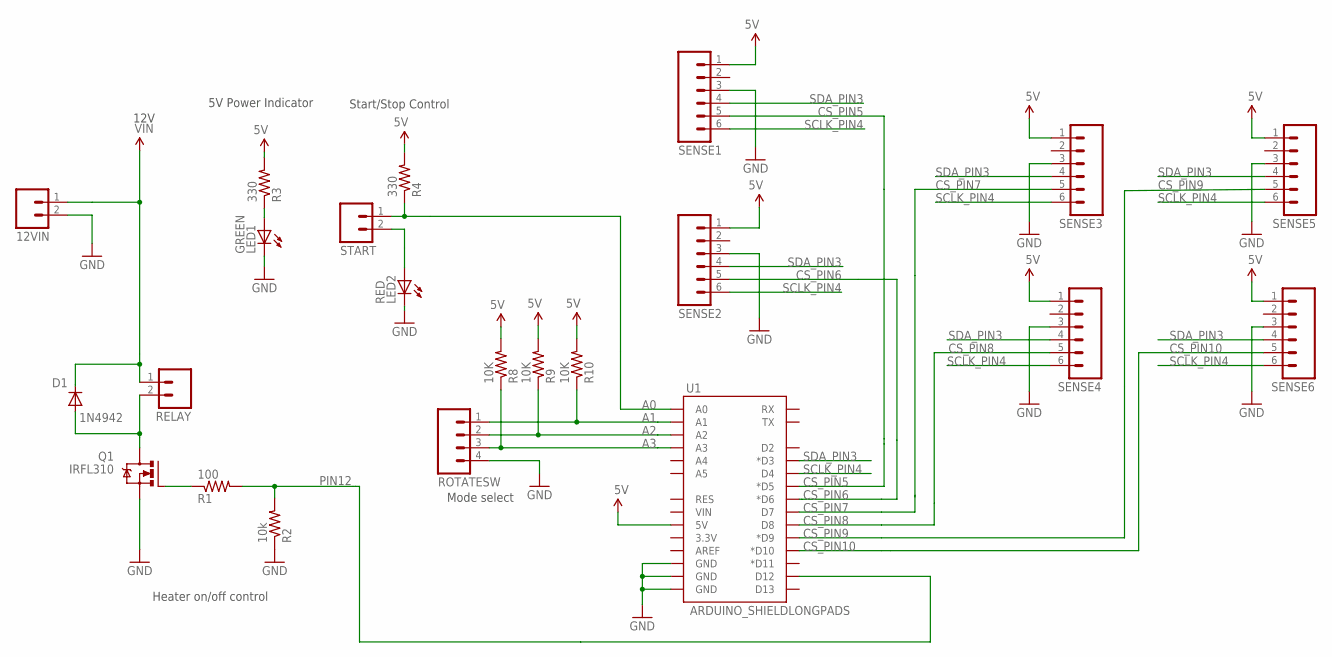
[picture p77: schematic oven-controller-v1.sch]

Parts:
12VIN: M023.5MM_LOCK; SCREWTERMINAL-3.5MM-2_LOCK
D1: 1N4942; DO41-10
LED1: GREEN; LED5MM
LED2: RED; LED5MM
Q1: IRFL310; TO220BV
R1: 100; V234/12
R2: 10k; V234/12
R3, R4: 330; 0207/10
R8, R9, R10: 10K; 0207/10
RELAY: M023.5MM_LOCK; SCREWTERMINAL-3.5MM-2_LOCK
ROTATESW: M04LOCK_LONGPADS; 1X04_LOCK_LONGPADS
SENSE1, SENSE2, SENSE3, SENSE4, SENSE5, SENSE6: M06LOCK_LONGPADS; 1X06_LOCK_LONGPADS
START: M023.5MM_LOCK; SCREWTERMINAL-3.5MM-2_LOCK
U1: ARDUINO_SHIELDLONGPADS; DUEMILANOVE_SHIELD_LONGPADS

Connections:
5V: R3.2, R4.2, R8.2, R9.2, R10.2, SENSE1.1, SENSE2.1, SENSE3.1, SENSE4.1, SENSE5.1, SENSE6.1, U1.5V
A0: R4.1, START.1, U1.A0
A1: R10.1, ROTATESW.1, U1.A1
A2: R9.1, ROTATESW.2, U1.A2
A3: R8.1, ROTATESW.3, U1.A3
CS_PIN5: SENSE1.5, U1.D5 (*D5)
CS_PIN6: SENSE2.5, U1.D6 (*D6)
CS_PIN7: SENSE3.5, U1.D7
CS_PIN8: SENSE4.5, U1.D8
CS_PIN9: SENSE5.5, U1.D9 (*D9)
CS_PIN10: SENSE6.5, U1.D10 (*D10)
GND: 12VIN.2, LED1.K (C), LED2.K (C), Q1.S, R2.1, ROTATESW.4, SENSE1.3, SENSE2.3, SENSE3.3, SENSE4.3, SENSE5.3, SENSE6.3, U1.GND@0 (GND), U1.GND@1 (GND), U1.GND@2 (GND)
unnamed: Q1.G, R1.1
unnamed: D1.A, Q1.D, RELAY.2
unnamed: LED2.A, START.2
unnamed: LED1.A, R3.1
PIN12: R1.2, R2.2, U1.D12
SCLK_PIN4: SENSE1.6, SENSE2.6, SENSE3.6, SENSE4.6, SENSE5.6, SENSE6.6, U1.D4
SDA_PIN3: SENSE1.4, SENSE2.4, SENSE3.4, SENSE4.4, SENSE5.4, SENSE6.4, U1.D3 (*D3)
VIN: 12VIN.1, D1.C, RELAY.1

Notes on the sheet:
Mode select
Heater on/off control
12V
Start/Stop Control
5V Power Indicator

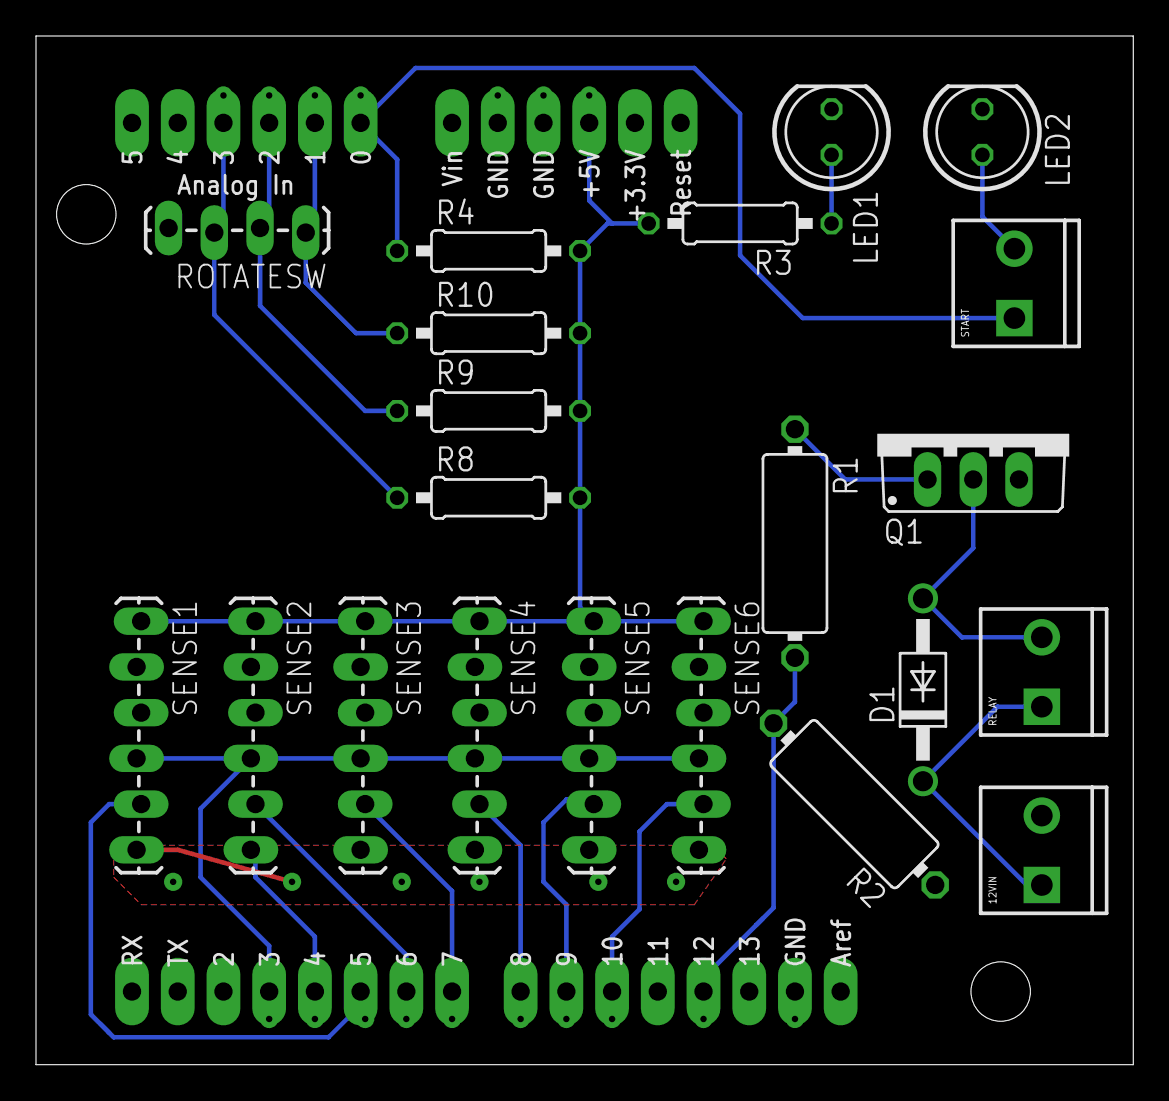
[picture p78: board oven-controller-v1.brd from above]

Board: 2 copper layers, 61.0 x 57.1 mm, 22 parts (0 on the bottom side), 20 nets.

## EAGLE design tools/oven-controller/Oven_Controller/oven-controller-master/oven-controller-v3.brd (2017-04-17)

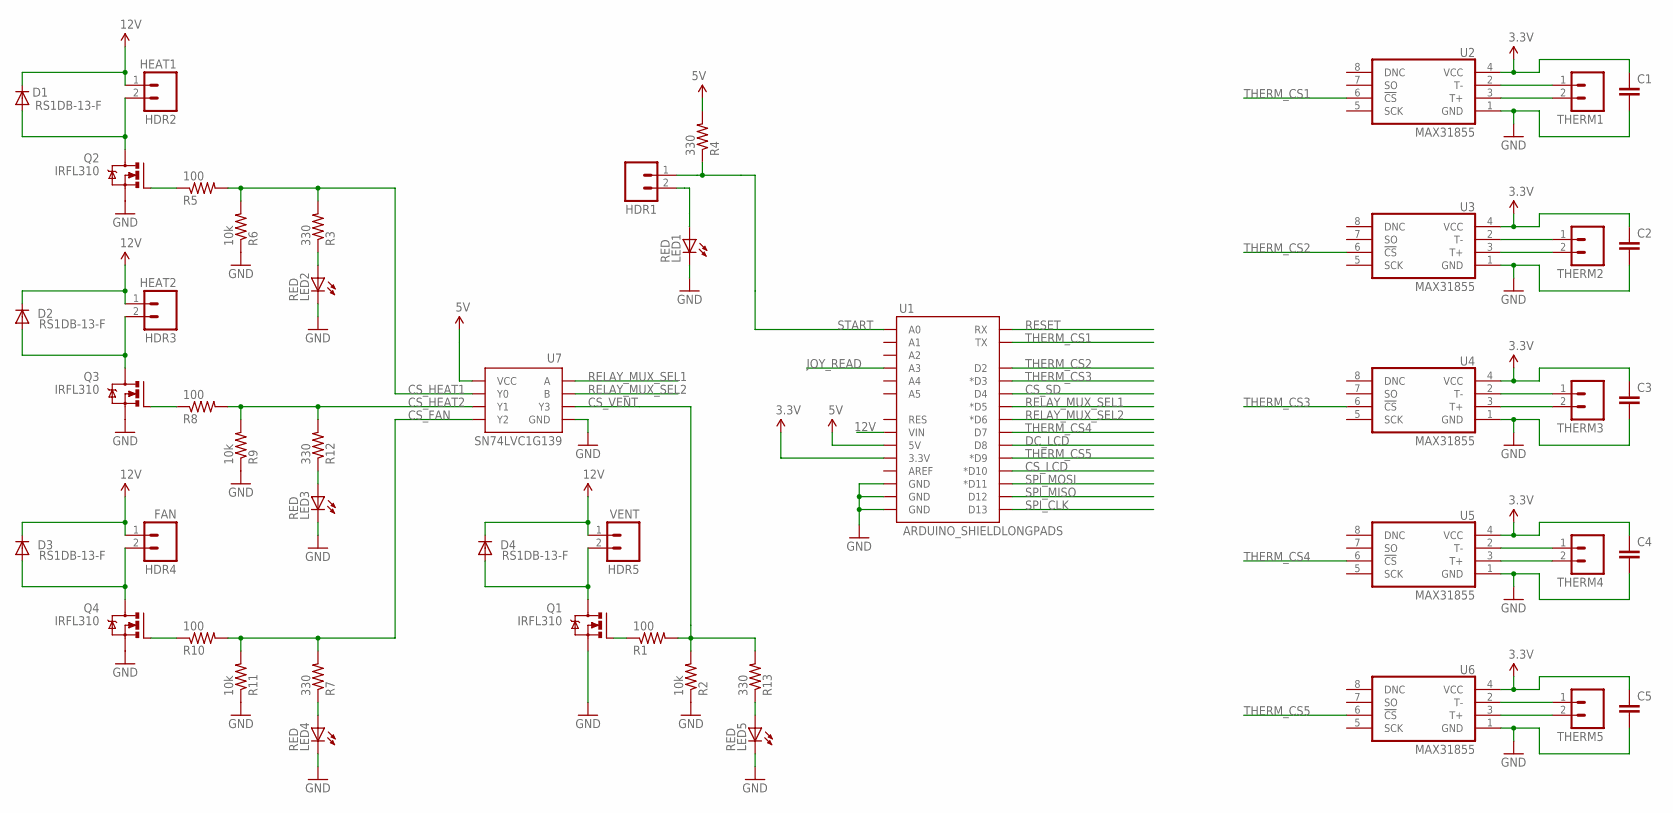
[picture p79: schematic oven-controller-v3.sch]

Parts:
C1, C2, C3, C4, C5: C-EUC0603K; C0603K
D1, D2, D3, D4: RS1DB-13-F; SMA-DIODE_ALT
HDR1: M023.5MM_LOCK; SCREWTERMINAL-3.5MM-2_LOCK
HDR2: HEAT1; SCREWTERMINAL-3.5MM-2_LOCK
HDR3: HEAT2; SCREWTERMINAL-3.5MM-2_LOCK
HDR4: FAN; SCREWTERMINAL-3.5MM-2_LOCK
HDR5: VENT; SCREWTERMINAL-3.5MM-2_LOCK
LED1, LED2, LED3, LED4, LED5: RED; LED-0603
Q1, Q2, Q3, Q4: IRFL310; TO220BV
R1, R5, R8, R10: 100; 0603-C-NOSILK
R2, R6, R9, R11: 10k; 0603-C-NOSILK
R3, R4, R7, R12, R13: 330; 0603-C-NOSILK
THERM1, THERM2, THERM3, THERM4, THERM5: M023.5MM_LOCK; SCREWTERMINAL-3.5MM-2_LOCK
U1: ARDUINO_SHIELDLONGPADS; DUEMILANOVE_SHIELD_LONGPADS
U2, U3, U4, U5, U6: MAX31855; SO-8
U7: SN74LVC1G139; 8LSSOP

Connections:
3.3V: C1.1, C2.1, C3.1, C4.1, C5.1, U1.3.3V, U2.4 (VCC), U3.4 (VCC), U4.4 (VCC), U5.4 (VCC), U6.4 (VCC)
5V: R4.2, U1.5V, U7.P$8 (VCC)
12V: D1.C, D2.C, D3.C, D4.C, HDR2.1, HDR3.1, HDR4.1, HDR5.1, U1.VIN
CS_FAN: R7.2, R10.2, R11.2, U7.P$5 (Y2)
CS_HEAT1: R3.2, R5.2, R6.2, U7.P$7 (Y0)
CS_HEAT2: R8.2, R9.2, R12.2, U7.P$6 (Y1)
CS_LCD: U1.D10 (*D10)
CS_SD: U1.D4
CS_VENT: R1.2, R2.2, R13.2, U7.P$3 (Y3)
DC_LCD: U1.D8
GND: C1.2, C2.2, C3.2, C4.2, C5.2, LED1.C, LED2.C, LED3.C, LED4.C, LED5.C, Q1.S, Q2.S, Q3.S, Q4.S, R2.1, R6.1, R9.1, R11.1, U1.GND@0 (GND), U1.GND@1 (GND), U1.GND@2 (GND), U2.1 (GND), U3.1 (GND), U4.1 (GND), U5.1 (GND), U6.1 (GND), U7.P$4 (GND)
HDR3: D3.A, HDR4.2, Q4.D
JOY_READ: U1.A3
unnamed: Q2.G, R5.1
unnamed: Q1.G, R1.1
unnamed: D4.A, HDR5.2, Q1.D
unnamed: D1.A, HDR2.2, Q2.D
unnamed: THERM1.1, U2.2 (T-)
unnamed: THERM1.2, U2.3 (T+)
unnamed: LED2.A, R3.1
unnamed: THERM2.1, U3.2 (T-)
unnamed: LED4.A, R7.1
unnamed: HDR1.2, LED1.A
unnamed: THERM2.2, U3.3 (T+)
unnamed: THERM3.1, U4.2 (T-)
unnamed: THERM3.2, U4.3 (T+)
unnamed: THERM4.1, U5.2 (T-)
unnamed: THERM4.2, U5.3 (T+)
unnamed: THERM5.1, U6.2 (T-)
unnamed: THERM5.2, U6.3 (T+)
unnamed: LED3.A, R12.1
unnamed: LED5.A, R13.1
unnamed: Q3.G, R8.1
unnamed: D2.A, HDR3.2, Q3.D
unnamed: Q4.G, R10.1
RELAY_MUX_SEL1: U1.D5 (*D5), U7.P$1 (A)
RELAY_MUX_SEL2: U1.D6 (*D6), U7.P$2 (B)
RESET: U1.RX
SPI_CLK: U1.D13
SPI_MISO: U1.D12
SPI_MOSI: U1.D11 (*D11)
START: HDR1.1, R4.1, U1.A0
THERM_CS1: U1.TX, U2.6 (!CS)
THERM_CS2: U1.D2, U3.6 (!CS)
THERM_CS3: U1.D3 (*D3), U4.6 (!CS)
THERM_CS4: U1.D7, U5.6 (!CS)
THERM_CS5: U1.D9 (*D9), U6.6 (!CS)

Board: 2 copper layers, 48 parts (0 on the bottom side), 39 nets, no tracks yet.

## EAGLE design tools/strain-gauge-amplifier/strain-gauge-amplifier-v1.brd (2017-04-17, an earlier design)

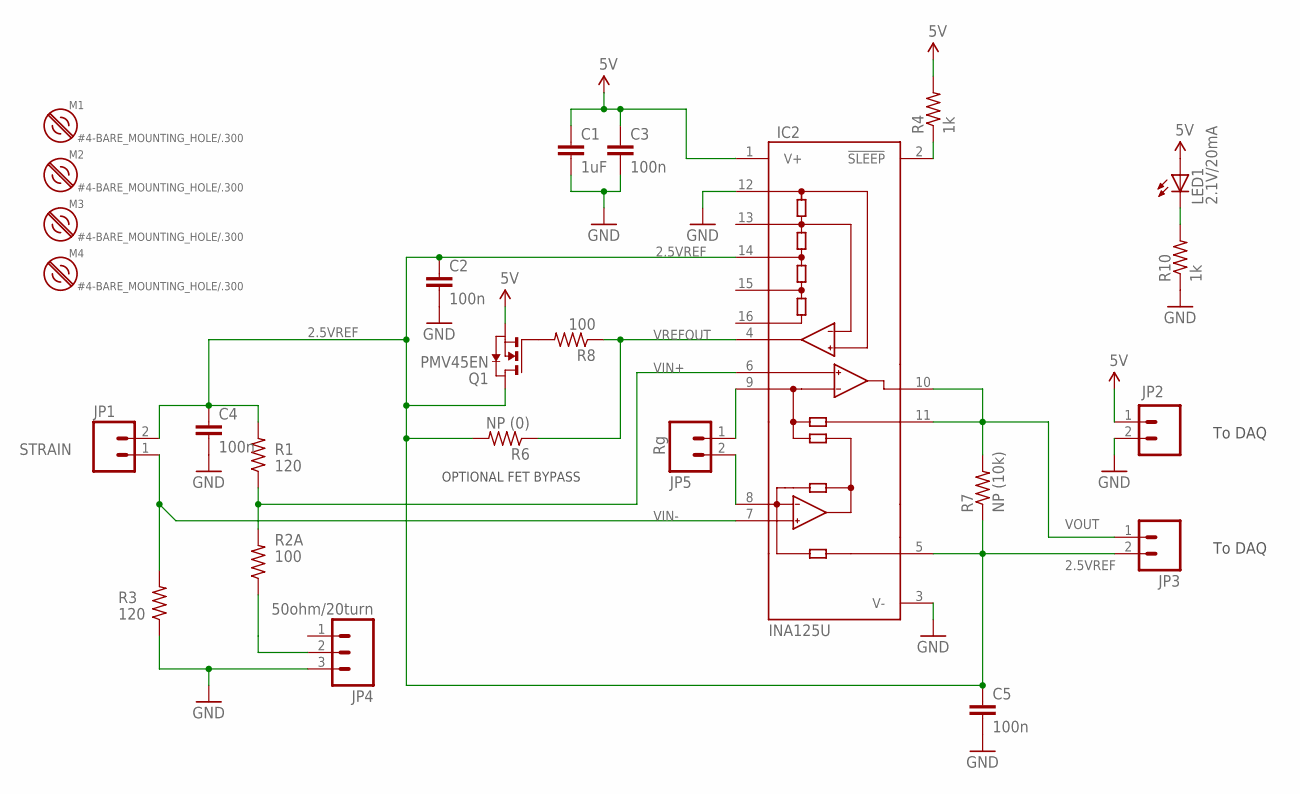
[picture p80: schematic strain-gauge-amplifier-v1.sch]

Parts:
C1: 1uF; 0805-C-NOSILK
C2, C3, C4, C5: 100n; 0805-C-NOSILK
IC2: INA125U; SO16-1
JP1: STRAIN; SCREWTERMINAL-5MM-2
JP2, JP3: M025MM; SCREWTERMINAL-5MM-2
JP4: 50ohm/20turn; 1X03_NO_SILK
JP5: Rg; SCREWTERMINAL-5MM-2
LED1: 2.1V/20mA; LED-0603
M1, M2, M3, M4: #4-BARE_MOUNTING_HOLE/.300; #4/.300-BARE+STD_NUT_OR_STAR_WASHER
Q1: PMV45EN; SOT23
R1, R3: 120; 0805-C-NOSILK
R2A, R8: 100; 0805-C-NOSILK
R4, R10: 1k; 0805-C-NOSILK
R6: NP (0); 0805-C-NOSILK
R7: NP (10k); 0805-C-NOSILK

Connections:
2.5VREF: C2.1, C4.1, C5.1, IC2.5 (REF), IC2.14 (REF2.5), JP1.2, JP3.2, Q1.3 (D), R1.2, R6.2, R7.1
5V: C1.1, C3.1, IC2.1 (V+), JP2.1, LED1.A, Q1.2 (S), R4.2
GND: C1.2, C2.2, C3.2, C4.2, C5.2, IC2.3 (V-), IC2.12 (REFCOM), JP2.2, JP4.3, R3.1, R10.1
unnamed: JP4.2, R2A.1
unnamed: IC2.9 (RG), JP5.1
unnamed: IC2.8 (RG), JP5.2
unnamed: Q1.1 (G), R8.2
unnamed: IC2.2 (!SLEEP), R4.1
unnamed: LED1.C, R10.2
VIN+: IC2.6 (+IN), R1.1, R2A.2
VIN-: IC2.7 (-VIN), JP1.1, R3.2
VOUT: IC2.10 (OUT), IC2.11 (SENSE), JP3.1, R7.2
VREFOUT: IC2.4 (REFOUT), R6.1, R8.1

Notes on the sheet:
OPTIONAL FET BYPASS
To DAQ

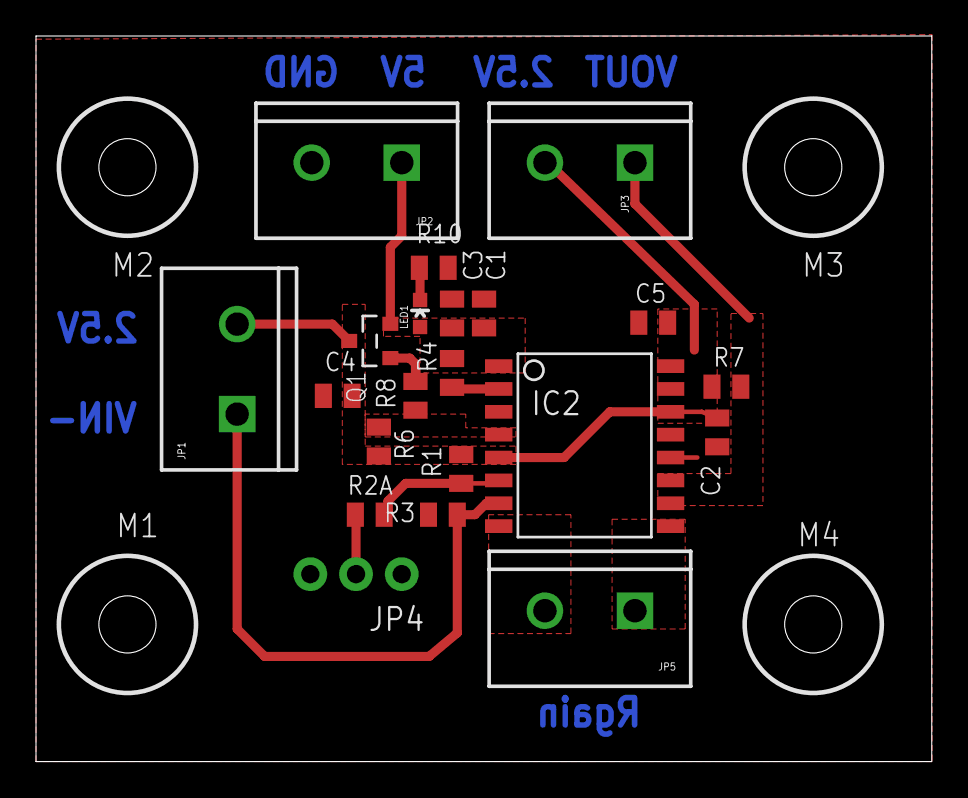
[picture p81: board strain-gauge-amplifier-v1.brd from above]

Board: 2 copper layers, 49.8 x 40.3 mm, 25 parts (0 on the bottom side), 13 nets.

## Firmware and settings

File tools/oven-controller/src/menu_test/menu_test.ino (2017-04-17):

/*******************************************************************
  This is a sketch to control the custom hardware for the Portland
  State MME Rocket Manufacturing Capstone curing oven controller. 

  It is heavily based on the example sketch for the Adafruit 1.8" 
  SPI display. The modifications are by 
  Jenner Hanni  <jeh.wicker@gmail.com>
  http://github.com/psas/mme-capstone/
  Released under MIT license.
  
  This sketch supports reading thermocouples, navigating a menu
  using the joystick, controlling relays to maintain temperature,
  and displaying relevant information about the oven on screen.

  It does not support the SD card!
  
  It includes Michael Margolis' Time library that provides a handy
  API for all the time-tracking. Super useful.
  http://www.pjrc.com/teensy/td_libs_Time.html
  
  TODO: 
  1. display the ramp or hold by looking at a temperature threshold
  2. stop the time if the switch is stopped
  3. add a ramp rate
  4. turn on particular heaters based on particular thermocouples
  
  *******************************************************************
  Original Adafruit notice:
  *******************************************************************
  
  This is an example sketch for the Adafruit 1.8" SPI display.
  This library works with the Adafruit 1.8" TFT Breakout w/SD card
  ---* http://www.adafruit.com/products/358
  as well as Adafruit raw 1.8" TFT display
  ---* http://www.adafruit.com/products/618
 
  Check out the links above for our tutorials and wiring diagrams
  These displays use SPI to communicate, 4 or 5 pins are required to
  interface (RST is optional)
  Adafruit invests time and resources providing this open source code,
  please support Adafruit and open-source hardware by purchasing
  products from Adafruit!

  Written by Limor Fried/Ladyada for Adafruit Industries.
  MIT license, all text above must be included in any redistribution
*********************************************************************/

#include <Adafruit_MAX31855.h> // Thermocouple library
#include <Adafruit_GFX.h>      // Core graphics library
#include <Adafruit_ST7735.h>   // Hardware-specific library
#include <SPI.h>
#include <Time.h>

#if defined(__SAM3X8E__)
    #undef __FlashStringHelper::F(string_literal)
    #define F(string_literal) string_literal
#endif

// Pins connection
int swReset       = 0;
int thermoCS1     = 1;
int thermoCS2     = 2;
int thermoCS3     = 3;
int sdCS          = 4;
int heater1       = 5;
int heater2       = 6;
int thermoCS4     = 7;
int lcdDC         = 8;
int thermoCS5     = 9;
int lcdCS         = 10;
int spiMOSI       = 11;
int spiMISO       = 12;
int spiCLK        = 13;
int swStart       = A0;
int fan           = A1;
int vent          = A2;
int joyRead       = A3;

#define OFF 0
#define ON 1

#define Neutral 0
#define Press 1
#define Up 2
#define Down 3
#define Right 4
#define Left 5

// this struct holds state information for use
// in the display menu's state machine 
struct aState {
  int cur;
  int nL;
  int nU;
  int nR;
  int nD;
  int nS;
};

// this struct contains info for a given step
// so the program can use an array of steps
struct stepInfo {
  int rate = 0;
  int temp = 0;
  int secs = 0;
  int elapsed = 0;
  int starttime = 0;
  int phase = 0; // 0 ramp, 1 hold
};

stepInfo steplist[9];
int maxStep = 1;    // total number of steps in a program
int curSetStep = 1; // set steps used by the menu display
int curRunStep = 0; // running steps used in oven control

// flags for knowing when to redraw when running the profile
int updateStepFlag = 0;
int reDisplayFlag = 0;
int doneFlag = 0;

// menu display is a finite state machine
// transitions come from joystick input
// see the documentation for the state diagram
aState states[18];
int curState;
int prevState;

// oven relay control status is enabled or disabled by start switch
int curstatus = OFF;

// current temperature in Fahrenheit
int curtemp = -1;
int prevtemp = -1;
int curtempflag = 0;
int tempThreshold = 5; // determines whether one or two heaters on/off
int thermStatus[5] = {0}; 
int numActiveThermocouples = 0;
int ADCThreshold = 100;

// tracking time using Margolis' time tracking library
time_t reftime = 0;
time_t nowtime = 0;
time_t prevmin = 0;
  
// settings
int ramprate = 1;
int holdtemp1 = 0;
int holdtemp2 = 0;
int holdtemp3 = 0;
int holdtimehour = 0;
int holdtimemins = 0;
int holdtimesecs = 0;

// global init of the LCD display and thermocouple
Adafruit_ST7735 tft = Adafruit_ST7735(lcdCS, lcdDC, spiMOSI, spiCLK, swReset);
Adafruit_MAX31855 thermocouple1(spiCLK, thermoCS1, spiMISO);
Adafruit_MAX31855 thermocouple2(spiCLK, thermoCS2, spiMISO);
Adafruit_MAX31855 thermocouple3(spiCLK, thermoCS3, spiMISO);
Adafruit_MAX31855 thermocouple4(spiCLK, thermoCS4, spiMISO);
Adafruit_MAX31855 thermocouple5(spiCLK, thermoCS5, spiMISO);

void setup(void) {


  Serial.begin(9600);
  Serial.println("\nENTERING SETUP\n");
  pinMode(LED_BUILTIN, OUTPUT);
  
  // Our supplier changed the 1.8" display slightly after Jan 10, 2012
  // so that the alignment of the TFT had to be shifted by a few pixels
  // this just means the init code is slightly different. Check the
  // color of the tab to see which init code to try. If the display is
  // cut off or has extra 'random' pixels on the top & left, try the
  // other option!
  // If you are seeing red and green color inversion, use Black Tab

  // set the reference for tracking time in seconds
  reftime = now();
  nowtime = now() - reftime;
  Serial.println(nowtime);
  Serial.println(reftime);
  Serial.println("run: ");
  
  int i = 0;
  
  // wait for MAX chips to stabilize
  delay(1500);
  setHeaters(OFF,OFF);

  // set heater, fan, and vent relay pins as outputs
  pinMode(heater1, OUTPUT);
  pinMode(heater2, OUTPUT);
  pinMode(fan, OUTPUT);
  pinMode(vent, OUTPUT);
  digitalWrite(heater1, LOW);
  digitalWrite(heater2, LOW);
  digitalWrite(fan, LOW);
  digitalWrite(vent, LOW);
  
  // init states array with state structs
  // {cur,L,U,R,D,S}
  states[0] = {0,0,0,1,2,0};
  states[1] = {1,0,1,1,1,1};
  states[2] = {2,2,0,6,3,6};
  states[3] = {3,3,2,4,5,4};
  states[4] = {4,4,4,4,4,3};
  states[5] = {5,5,3,5,5,0};
  states[6] = {6,6,6,7,8,6};
  states[7] = {7,6,7,7,7,7};
  states[8] = {8,8,6,9,10,8};
  states[9] = {9,8,9,9,9,9};
  states[10] = {10,10,8,11,14,10};
  states[11] = {11,10,11,12,11,11};
  states[12] = {12,11,12,13,12,12};
  states[13] = {13,12,13,13,13,13};
  states[14] = {14,14,10,15,17,13};
  states[15] = {15,14,15,16,15,15};
  states[16] = {16,15,16,16,16,16};
  states[17] = {17,17,14,17,17,2};
  
  // Our TFT display had a Green Tab so we use blacktab, it seems to work.
  tft.initR(INITR_BLACKTAB);   // initialize a ST7735S chip, black tab

  tft.setRotation(135);
  tft.fillScreen(ST7735_WHITE);
  tft.setTextColor(ST7735_BLACK);
  tft.setTextWrap(false);

  curstatus = CheckStartButton();

  curState = 0;
  redrawMenu(0);
  displayMenu(curState);
  
  hackySPIfix();

  // get active thermocouples
  // disregard values from therm X if therm[X] = 1
  // It's good to know when a TCP is unplugged, but this seems to be begging
  // to make a bug... Think about what happens if someone wants to validate
  // the controller readings and starts up the controller with the TCP in 
  // an ice-water bath, lol.
  if ((int)thermocouple1.readFarenheit() == 32) thermStatus[1] = 1;
  if ((int)thermocouple2.readFarenheit() == 0) thermStatus[2] = 1;
  if ((int)thermocouple3.readFarenheit() == 0) thermStatus[3] = 1;
  if ((int)thermocouple4.readFarenheit() == 32) thermStatus[4] = 1;
  if ((int)thermocouple5.readFarenheit() == 32) thermStatus[5] = 1;
    
  // get number of active thermocouples for the averaging
  int j;
  for (j = 1; j <= 5; j++) {
    if (thermStatus[j] == 0) {
      numActiveThermocouples++;
    }
  }
  
}

void loop() {
  Serial.println("\nENTERING LOOP\n");
    digitalWrite(LED_BUILTIN, HIGH);   // turn the LED on (HIGH is the voltage level)
  delay(1000);                       // wait for a second
  digitalWrite(LED_BUILTIN, LOW);    // turn the LED off by making the voltage LOW
  delay(1000);                       // wait for a second


  // check start button
  curstatus = CheckStartButton();
  
  // check joystick
  int joy = CheckJoystick();
  
  // handle joystick movement 
  if (joy != 0) {
    prevState = curState;
    curState = handleJoystick(joy);

    displayMenu(curState);
    delay(100);
  }

  if (curState == 4) {
    // handle relays
    // if temp is below step temp, turn on heaters
    // if temp is above step temp, turn off heaters
    if (curstatus == ON)  
      updateHeaters();
      
    // update run screen
    displayMenu(curState);
    
  }

  // check thermocouples and get average value
  // TODO: turn on particular heaters based on particular thermocouples
  // TODO: Figure out proper temperature averaging when some TCPs are unplugged!
  curtemp = thermocouple2.readFarenheit();
  // curtemp = 0;
  // if (thermStatus[1] == 0)
  //   curtemp += thermocouple1.readFarenheit();
  // Serial.print(curtemp);
  // Serial.print(" ");
  // if (thermStatus[2] == 0)
  //   curtemp += thermocouple2.readFarenheit();
  // Serial.print(curtemp);
  // Serial.print(" ");
  // if (thermStatus[3] == 0)
  //   curtemp += thermocouple3.readFarenheit();
  // Serial.print(curtemp);
  // Serial.print(" ");
  // if (thermStatus[4] == 0)
  //   curtemp += thermocouple4.readFarenheit();
  // Serial.print(curtemp);
  // Serial.print(" ");
  // if (thermStatus[5] == 0)
  //   curtemp += thermocouple5.readFarenheit();
  // Serial.print(curtemp);
  // Serial.print(" ");
  // curtemp = curtemp / numActiveThermocouples;
  Serial.println("thermocouple1.readFarenheit()");
  Serial.println(thermocouple1.readFarenheit());
  Serial.println("thermocouple2.readFarenheit()");
  Serial.println(thermocouple2.readFarenheit());
  Serial.println("thermocouple3.readFarenheit()");
  Serial.println(thermocouple3.readFarenheit());
  Serial.println("thermocouple4.readFarenheit()");
  Serial.println(thermocouple4.readFarenheit());
  Serial.println("thermocouple5.readFarenheit()");
  Serial.println(thermocouple5.readFarenheit());
  Serial.println("curtemp");
  Serial.println(curtemp);
  
  // if the temp has incremented, update temp
  // only do this in main screen or in run screen
  if (curtemp != prevtemp) { 
    prevtemp = curtemp; 
    curtempflag = 1;
    updateNum(70,98,20,10,curtemp);
  }

}

// Set the first and second heaters to ON or OFF.
void setHeaters(int val1, int val2) {
  digitalWrite(heater1, val1);  
  delay(100);
  digitalWrite(heater2, val2);  
  delay(100);
}

void updateHeaters() {
  // Previously, this activated only one relay if within +1 threshold of 
  // the target temp. However, the oven is only set up for one relay, so it 
  // would just keep heating until one threshold above the target temp. 
  // What's worse, there's a delay between the input of heat and the rise 
  // of the voltage on the thermocouple, so the oven consistently overshot 
  // its temperature!
  if (curtemp < steplist[curRunStep].temp - tempThreshold) 
    setHeaters(ON,ON);
  else
    setHeaters(OFF,OFF);
}

void hackySPIfix() {
  tft.fillRect(0,0,1,1,ST7735_WHITE);
}

int CheckStartButton() {
  
  int prevstatus = curstatus;
  uint8_t startButton = analogRead(swStart);
  if (startButton < ADCThreshold) 
    curstatus = ON;
  else curstatus = OFF;
  
  if (prevstatus != curstatus) {
    redrawMenu(0);
    displayMenu(curState);
  }
  return curstatus;
  
}
// Check the joystick position
int CheckJoystick()
{
  int joystickState = analogRead(3);
  
  if (joystickState < 50) return Left;
  if (joystickState < 150) return Down;
  if (joystickState < 250) return Press;
  if (joystickState < 500) return Right;
  if (joystickState < 650) return Up;
  return Neutral;
}

// get the data out of the selected step in the array
// so we can display the data for that step on the screen
void getStep(int i) {
  ramprate = steplist[i].rate;
  if (ramprate == 0) ramprate = 1;
  holdtemp1 = (steplist[i].temp/100) % 100;
  holdtemp2 = (steplist[i].temp/10) % 10;
  holdtemp3 = steplist[i].temp % 10;
  holdtimesecs = steplist[i].secs;
  holdtimehour = (holdtimesecs/3600) % 3600;
  holdtimemins = (holdtimesecs/60) % 60;
}

// store the values of the selected step in the array
void setStep(int i) {
  steplist[i].rate = ramprate;
  steplist[i].temp = holdtemp1*100 + holdtemp2*10 + holdtemp3;
  steplist[i].secs = holdtimehour*3600 + holdtimemins*60;
}

int handleJoystick(int joy) {
  switch (joy) {
    case Left:
      if (curState == 9 || curState == 11 || curState == 15)
            setStep(curSetStep);
      return states[curState].nL;
      break;
    case Right:
      return states[curState].nR;
      break;
    case Up:
      switch(states[curState].nU) {
        case 1:
          if (maxStep > 0 && maxStep < 9) {
            maxStep++;
            updateNum(130,20,12,10,maxStep);
          }
          break;
        case 7:
          if (curSetStep < maxStep) {
            curSetStep++;
            getStep(curSetStep);
            redrawMenu(1);
          }
          break;
        case 9:
          if (ramprate < 9) {
            ramprate++;
            updateNum(77,35,12,10,ramprate);
          }
          break;
        case 11:
          if (holdtemp1 < 9) {
            holdtemp1++;
            updateNum(77,50,5,10,holdtemp1);
          }
          break;
        case 12:
          if (holdtemp2 < 9) {
            holdtemp2++;
            updateNum(83,50,5,10,holdtemp2);
          }
          break;
        case 13:
          if (holdtemp3 < 9) {
            holdtemp3++;
            updateNum(89,50,5,10,holdtemp3);
          }
          break;
        case 15:
          if (holdtimehour < 9) {
            holdtimehour++;
            updateNum(77,65,5,10,holdtimehour);
          }
          break;
        case 16:
          if (holdtimemins < 59) {
            holdtimemins++;
            updateNum(95,65,40,10,holdtimemins);
          } 
          break;
        }
      return states[curState].nU;
      break;

    case Down:
      switch(states[curState].nD) {
        case 1:
          if (maxStep > 1 && maxStep < 10) {
            maxStep--;
            updateNum(130,20,12,10,maxStep);
          }
          break;
        case 7:
          if (curSetStep > 1) {
            curSetStep--;
            getStep(curSetStep);
            redrawMenu(1);
          }
          break;
        case 9:
          if (ramprate > 1) {
            ramprate--;
            updateNum(77,35,12,10,ramprate);
          }
          break;
        case 11:
          if (holdtemp1 > 0) {
            holdtemp1--;
            updateNum(77,50,5,10,holdtemp1);
          }
          break;
        case 12:
          if (holdtemp2 > 0) {
            holdtemp2--;
            updateNum(83,50,5,10,holdtemp2);
          }
          break;
        case 13:
          if (holdtemp3 > 0) {
            holdtemp3--;
            updateNum(89,50,5,10,holdtemp3);
          }
          break;
        case 15:
          if (holdtimehour > 0) {
            holdtimehour--;
            updateNum(77,65,5,10,holdtimehour);
          }
          break;
        case 16:
          if (holdtimemins > 0) {
            holdtimemins--;
            updateNum(95,65,40,10,holdtimemins);
          } 
          break;
      }
      return states[curState].nD;
      break;
      
    case Press:
      if (curState == 17)
            setStep(curSetStep);
      return states[curState].nS;
      break;
      
  }
  delay(100);
}
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

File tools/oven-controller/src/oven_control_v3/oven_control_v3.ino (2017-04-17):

/********************************************

 This is oven control shield code v3 written by 
 Thanh Tung Nguyen and Jenner Hanni, 2014. 
 http://github.com/wicker/oven-controller/
 
 This is an oven control sketch for the Adafruit 1.8" TFT
 shield with joystick stacked on a PSAS Airframes Team 
 Oven Control Shield v3 stacked on an Arduino Uno.
 
 Our LCD shield is the BLACKTAB version.
 
 The display, SD card, and five MAX31855 thermocouple-
 to-digital chips are all on the SPI bus. The SD card 
 also uses the SD library. 
 
 We referenced code written by Limor Fried/Ladyada
 for Adafruit Industries under the MIT license.

 GENERIC TODO: Everything related to SD card.
 Otherwise look for TODO notes in comments.
 
 *******************************************/
  
#include <Adafruit_MAX31855.h>
#include <Adafruit_ST7735.h>
#include <Adafruit_GFX.h>
#include <SD.h>
#include <SPI.h>

#define OFF 0
#define ON  1

// assign state values
#define START   1
#define RUNNING 2
#define STOP    3
#define STOPPED 4

// assign joystick positions
#define BUTTON_NONE 0
#define BUTTON_DOWN 1
#define BUTTON_RIGHT 2
#define BUTTON_SELECT 3
#define BUTTON_UP 4
#define BUTTON_LEFT 5

// Pins connection
int swReset       = 0;
int thermoCS1     = 1;
int thermoCS2     = 2;
int thermoCS3     = 3;
int sdCS          = 4;
int heater1       = 5;
int heater2       = 6;
int thermoCS4     = 7;
int lcdDC         = 8;
int thermoCS5     = 9;
int lcdCS         = 10;
int spiMOSI       = 11;
int spiMISO       = 12;
int spiCLK        = 13;
int swStart       = A0;
int fan           = A1;
int vent          = A2;
int joyRead       = A3;

// initialize the LCD screen
Adafruit_ST7735 tft = Adafruit_ST7735(lcdCS, lcdDC, swReset);

// shouldn't these be #defines or at least const double, const int, etc?
double tempSet         =  350;        // farenheit
double tempInc         =  3 ;         // Temperature increament per minutes
double tempErrRange    =  0;
double tempThreshold   =  3;          // Temperature limit to turn on both heaters
int ADCThreshold       =  900;
int timeDelay          =  5000;
float timeMax          =  12780;      // (sec) timeMax=time_ramping+time_at_350; (set at 2 hours), initial temp: 70*F
bool statusFlag        = 0;

// calibration 
double sensor1  =  0;
double sensor2  =  -4;
double sensor3  =  0;
double sensor4  =  0;
double sensor5  =  0;

// variables
double tempErr;
double tempSensor1;
double tempSensor2;
double tempSensor3;
double tempSensor4;
double tempSensor5;
double tempAverage;
double tempInitial;         // room temp

double currTempSet;
double tempSetLow;
double tempSetHigh;

double startTime;
double currTime;

uint8_t buttonhistory  =  0;
uint8_t joystickVal = 0;

// Thermocouples
Adafruit_MAX31855 thermocouple1(spiCLK, thermoCS1, spiMISO);
Adafruit_MAX31855 thermocouple2(spiCLK, thermoCS2, spiMISO);
Adafruit_MAX31855 thermocouple3(spiCLK, thermoCS3, spiMISO);
Adafruit_MAX31855 thermocouple4(spiCLK, thermoCS4, spiMISO);
Adafruit_MAX31855 thermocouple5(spiCLK, thermoCS5, spiMISO);

// Set the first and second heaters to ON or OFF.
void set_heaters(int val1, int val2) {
  digitalWrite(heater1, val1);  // turn off the heaters
  delay(100);
  digitalWrite(heater2, val2);  // turn off the heaters
  delay(100);
}

// Read the joystick and save the value in joystickVal.
void read_joystick() {

  float a = analogRead(3);

  a *= 5.0;
  a /= 1024.0;
  
  Serial.print("Button read analog = ");
  Serial.println(a);
  if (a < 0.2) joystickVal = BUTTON_DOWN;
  if (a < 1.0) joystickVal = BUTTON_RIGHT;
  if (a < 1.5) joystickVal = BUTTON_SELECT;
  if (a < 2.0) joystickVal = BUTTON_UP;
  if (a < 3.2) joystickVal = BUTTON_LEFT;
  else         joystickVal = BUTTON_NONE;
}

// Read the start button and update the state machine.
// Possible states are START, RUNNING, STOP, and STOPPED.
// The state is updated and the timer is incremented or
// reset to zero, depending on state.
//
// Possibly better to rename this update_state_machine().
void handle_start_button() {

  uint8_t ADCReading;

  // if the input is HIGH, handle it as a START
  if (ADCReading > ADCThreshold) {
    if (statusFlag == START) {
      statusFlag = RUNNING;
      // set start time
      startTime = millis(); 
      currTime = millis()-startTime;
      // set start temperature
      check_temp_sensors();
      tempInitial = tempAverage;
    }
    else if (statusFlag == RUNNING) {
      // check if timer has reached end of profile time
      if (currTime/1000 >= timeMax)
        statusFlag = STOP;
      else
        statusFlag = RUNNING;
      currTime = millis()-startTime;
    }
    else if (statusFlag == STOP) {
      statusFlag = STOPPED;
      currTime = 0;
    }
    else { 
      statusFlag = START;
      currTime = 0;
    }
  }

  // otherwise the input is LOW, handle it as a STOP
  else {
    if (statusFlag == START) {
      statusFlag = STOP;
      currTime = millis()-startTime;
    }
    else if (statusFlag == RUNNING) {
      statusFlag = STOP;
      currTime = millis()-startTime;
    }
    else if (statusFlag == STOP) {
      statusFlag = STOPPED;
      currTime = 0;
    }
    else { 
      statusFlag = STOPPED;
      currTime = 0;
    }
  }
}

// Poll each thermocouple value and get an average value.
// Adjusting by 32 for each tempSensor value
// eliminates the SPI disconnection.
void check_temp_sensors() {
  float tempSum=0;
  int count=0;
  tempSensor1 = thermocouple1.readFarenheit()+sensor1;
  if (tempSensor1>32) {
    count=count+1;
    tempSum=tempSum+tempSensor1;
  }
  delay(10);
  tempSensor2 = thermocouple2.readFarenheit()+sensor2;
  if (tempSensor2>32) {
    count=count+1;
    tempSum=tempSum+tempSensor2;
  }
  delay(10);
  tempSensor3 = thermocouple3.readFarenheit()+sensor3;
  if (tempSensor3>32) {
    count=count+1;
    tempSum=tempSum+tempSensor3;
  }
  delay(10);
  tempSensor4 = thermocouple4.readFarenheit()+sensor4;
  if (tempSensor4>32) {
    count=count+1;
    tempSum=tempSum+tempSensor4;
  }
  delay(10);
  tempSensor5 = thermocouple5.readFarenheit()+sensor5;
  if (tempSensor5>32) {
    count=count+1;
    tempSum=tempSum+tempSensor5;
  }
  delay(10);
  tempAverage = tempSum/count;
}

// TODO: FIGURE THIS OUT AND EXPLAIN IT BETTER
// Not sure exactly what this is doing.
// It's deciding how to update the heaters, anyway.
// This really ought to take the state use it.
void update_heaters(int state) {
  currTempSet=min(350, currTime/1000/60*tempInc+tempInitial);
  tempSetLow= currTempSet-tempErrRange;
  tempSetHigh= currTempSet+tempErrRange;  

  if (tempAverage < tempSetLow && tempAverage > 32) {
    if (tempAverage < tempSetLow - tempThreshold) 
      set_heaters(ON,ON);
    else 
      set_heaters(ON,OFF);
  }
  else {
    if (tempAverage > tempSetHigh + tempThreshold)
      set_heaters(OFF,OFF);
    else 
      set_heaters(OFF,ON);
  }
}
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

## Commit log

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2014-03-07 Fixed FET resistors. Passes ERC, DRC. Needs review.
    [oven-controller-v3.brd, oven-controller-v3.sch]
2014-03-07 Cleaned up schematic, fixed a minor errors, ready for layout!
    [strain-gauge-amplifer-v1.sch]
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2014-03-07 Amplifier is now spelled correctly.
    [oven-controller-v3.sch, strain-gauge-amplifier-v1.brd, strain-gauge-amplifier-v1.sch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]
2014-03-08 Cleaned up board a bit - mostly made things wider, cleaned up one part placement.
    [strain-gauge-amplifier-v1.brd, strain-gauge-amplifier-v1.sch, strain-gauge-amplifier-v1.xls]
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2014-03-12 Fixed to strain gauge boards (doh!) and new readme file.
    [strain-gauge-amplifier-v2.brd, strain-gauge-amplifier-v2.sch]
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2014-03-16 Fixed diode package.
    [oven-controller-v3.brd, oven-controller-v3.sch]
2014-03-26 Lots of fixes. Reviewed. Passes ERC, DRC, rats. Ship it.
    [oven-controller-v3.brd, oven-controller-v3.sch]
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2014-08-06 airfoiled railbuttons
    tah dah... Dave please verify the launch rail dimensions for me
    [large rail buttons.SLDPRT]
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2015-04-15 added RCS module to cad design
    and changed the name of LV3.0 to BFR3.0
    [Fin_Section.SLDASM, PSAS-LV3.0-Antenna_Module_Top_Asm.SLDASM, PSAS-LV3.0-Motor_Section_Top_Asm.SLDASM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]
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2015-04-16 removed old assembly file
    removed old assembly file to avoid confusion.
    [Module_ASSY.SLDASM]
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2015-06-11 adjusted the weights of some of the parts to make them more accurate
    [Fin_060114_v2.SLDPRT, Fin_Section.SLDASM, PSAS-LV3.0-Antenna_Module_Top_Asm.SLDASM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]
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2016-03-13 optimized spline point placement
    This script is meant to find the optimal placement of an extra spline point for the LV3 nose cone. The curvature of the LD-Haack shape near the tip creates a large error when using evenly distributed sample points to approximate the shape using spline curves. This script compares different placements of an extra sample point, to minimize that error.
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2016-05-26 made a model to compensate for fin mistake; rearranged ORK files
    It turns out that the fins - which no-one was given a chance to review
    before they were sent out for manufacturing - have a major flaw: they
    are about 70% as long as they're supposed to be. (wow!) This is in
    addition to the concerns about the root fillet, which were also closed
    to review before machining.
    This means that the CoP is now much farther forward than designed. To
    compensate for this, we need to add about 6 kg of lead to the end of the
    nose cone! (This moves the CoM further forward.) Otherwise, the rocket will spin around and crash.
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2016-07-06 added the too-short fin frame CAD
    [shortFinJig.SLDPRT, shortFins.SLDPRT]
2016-07-06 Added corrected fin design with crude drag sim
    [LongFins.SLDPRT]
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2016-07-07 Modified the fin sweep to match OpenRocket
    Normally, sweep angle is defined as the angle (from perpendicular) of the line following the middle of the airfoil.
    (That's the "correct" definition, and is more-or-less what was used in the model.)
    In OpenRocket, it's defined as the angle (from perpendicular) of the leading edge.
    (Alternatively, OR lets you define the sweep length of the fin: how far the start of the tip is behind the start of the root.)
    I changed it to be defined by the sweep length and fixed a problem that made with extruding the rear truss.
    [LongFins.SLDPRT]
2016-07-07 Added fillet, updated drag force, applied mesh control, next step: weight reduction
    [LongFins.SLDPRT, shortFins.SLDPRT]
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2016-07-20 modified nose mold to accommodate recovery system
    increased the cylindrical section from 2 in to 8 in
    increased the nose hole diameter to 1 in
    made a slight change in the defining dimensions of the nose tip
    [vonKarman_asp5_negativeHalfMold_V2-3.SLDPRT]
2016-07-25 Strengthened front/back of mold; added index holes; added a ruler
    [vonKarman_asp5_negativeHalfMold_V2-3.SLDPRT]
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2016-07-26 continued the flutter analysis using R
    I'm taking a little while to get up to speed with python, so I just did
    it in a language I'm more familiar with.
    The HTML file is what you want to look at.
    [L-13a_ideal_0.0625fins.csv, L-13a_ideal_0.09375fins.csv, L-13a_ideal_0.125fins.csv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]
2016-07-29 most of the modifications requested by Alex Chally
    still need to add indexing holes, fixturing holes, and optional flange
    holes
    [vonKarman_asp5_negativeHalfMold_V2-3.SLDPRT]
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2016-08-05 Updated 1/8 Al. rail system; Added 1/16 Al. system option; Created CubeSat model
    [3UCubeSat.SLDPRT, RailAssem.SLDASM, RailAssemThin.SLDASM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]
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2016-08-12 description of the basic design and bibliography
    Next:
    add diagram/picture of the sandwich design;
    add more detailed description of the modules
    add pictures of the compressive failure
    add pictures of the puncture failure
    add CAD render of the cylindrical modules and/or whole rocket (this
    might not be worth it, since it's not currently made)
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2016-09-08 Updated assembly; Added mounts; TODO: Edit mounts to make room for new bolt holes; Edit rail length
    [PCCradleRailFIBER.SLDPRT, PCCradleRailSHORT.SLDPRT, PCCradleTopOPEN.SLDPRT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]
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2016-09-09 Finalized assembly; Added mounting holes; Added laser cutting print for center ribbing
    [PCCradleRailFIBER.SLDPRT, PCCradleTop.SLDPRT, RailAssemCradleOpenMiddle.SLDDRW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]
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2016-09-11 Removed old files and added to archive; Added more 60W drawings; Moved drawings to own folder
    [Cradle_lid_attachment_II.SLDPRT, DrawingExpl.SLDDRW, DrawingExpl.SLDPRT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]
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2016-09-25 Changed the minor diameter of the internal threads for the nosecone tip and nose plug.
    [noseplug.SLDPRT, noseplug_extended_cyl.SLDPRT, von_karmon_nose_tip2.SLDPRT]
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2016-09-28 Added even more laser cutting files; Added the new rail to be cut
    [1_JigVert.SLDDRW, 2_JigHoriz.SLDDRW, 3_RailHalf.SLDDRW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]
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2016-10-12 Added sim file for cradle v1; Added assembly for cradle v2; Performed static torsion test on cradle v1; Added technical drawing of interface ring
    [CradleInterface_TechDrawing.SLDDRW, Cradle_lid_attachment_II.SLDPRT, Cradle_lid_attachment_II_V2.SLDPRT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]
2016-10-12 Updated V2 Assem; Included V2 CubeSat (2U); Modified Interface ring for strength and weight
    [Cradle_lid_attachment_II.SLDPRT, PCCradleCurvedReinforce.SLDPRT, PCCradleTopOPEN_V2.SLDPRT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]
2016-10-13 Updated torsion sim mesh; Updated sim CAD files; Fixed filleting of center rings
    [PCCradleCurvedReinforce.SLDPRT, PCCradleTopOPEN_V2.SLDPRT, PCCradleTop_V2.SLDPRT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]
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2016-12-18 added the RCS ring to the main assembly
    Still need to add :
    * guts for the RCS
    * guts for the eNSR
    * recovery system
    * motor
    We (PSAS) should also try to figure out some way of saving our SW
    files so that SW doesn't keep touching the originals when we put them
    in an assembly. It makes it hard to tell what's ACTUALLY been changed.
    [LV3.SLDASM, Module18.SLDASM, Module24.SLDASM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]
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2016-12-20 Updated LV3 Assembly w/ cradle and motor frame; Still need fin-to-fincan in assembly
    [Fiberglass antenna module Sleeve.SLDPRT, PCCradleCurvedReinforce.SLDPRT, PCCradleTopOPEN_V2.SLDPRT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]
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2016-12-23 RCS was upside down, now fixed
    [LV3.SLDASM, Module18.SLDASM, Module24.SLDASM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]
2017-01-10 possible geometry for the big mold
    used to make a negative mold with carbon fiber
    [vonKarman_asp5_positiveHalfMold_V2-3.SLDPRT]
2017-01-10 Updated railsled design ready to be tested on the rail. Will update again if the prototype I built doesn't fit right.
    [90273A247_ZINC-PLATED STL FLAT HEAD PHIL MACHINE SCREW.SLDPRT, 91771A246_18-8 SS FLAT HEAD PHILLIPS MACHINE SCREW.SLDPRT, LV3_rail_sled 002-004.SLDDRW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]
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2017-01-25 made fin jig to accept rail sled; layup assembly
    TODO:
    * complete layup assembly for the fin can
    * update fin jig drawing to match these changes
    [LongFin.SLDASM, LongFins_ALedge.SLDPRT, Module18.SLDASM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]
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2017-02-25 possible workarounds to controller bugs
    [menu_test.ino]
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2017-03-28 completed fin can layup assembly
    Major things to note:
    * I changed the "T" block for the sled to give some room for the
    adhesive sheet and some spring washers.
    * I added a baseplate (intended to be made out of MDF). It interfaces
    with the female ring to align the module to the fins in the
    theta-direction. It also has 3 holes for leveling feet and a center hole
    that we could potentially run a 1/4" rod through (with the intent of
    attaching that rod to a spider on the other end, so we can fix the
    module to the baseplate).
    * I put in some PTFE tubes that have been cut in half. These sit between
    the leading/trailing edges and the jigs. This way, we can still controll
    the axial position of the fin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
    [PTFE_finShield.SLDPRT, allThread_quarterInch.SLDPRT, allThread_quarterInch_feet.SLDPRT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]
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2017-03-30 fixed some dimensiones with too-few digits
    [fin_jig_mid_TechDrawing.SLDDRW, fin_jig_top_bottom2_TechDrawing.SLDDRW]
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2017-04-16 Additing a basic CAD of the sanding module
    I am working on trying to put together a sanding setup for the modules. This is a caveman-like-CAD of the setup.
    [Sanding Lathe.dwg]
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2017-04-18 Organized folders; Archived old files; Cleared up names; Cleaned up assembly; Added laser cutting files
    [100211587UGM000_B.2.sldprt, 100211647UGM000_B.1.sldprt, 1521020X601XXX_100210424MOD000B.prt.1.sldprt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]
2017-04-18 Added cradle sub-assembly; Pointed assembly to correct files
    [LV3.SLDASM]
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2017-05-16 Uploaded the spacer for ensuring CubeSat is flush with the cradle end
    [CradleAssem.SLDASM, SpacerWall.SLDPRT]
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2017-05-23 dummy tip, new nose plug; replaced old shell
    The dummy tip helps with installing the nose plug and making sure the
    tip-to-shell transition is smooth. The plug holds the tip onto the
    nosecone. The shell that I'd put into the assembly was the 2014 shell,
    not the current shell.
    [dummyNoseTip.SLDDRW, dummyNoseTip.SLDPRT, jenkyNoseTip.SLDDRW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]
2017-05-23 removed old shell and tip
    Need to go through and identify remaining old files...
    [noseShell.SLDPRT, von_karmon_nose _tip.SLDPRT]
2017-05-23 aluminum form for creating two fin brackets
    It would be a good idea to redesign this to use two smaller pieces of
    aluminum, rather than hogging out a giant bar...
    [bracketForm_double.SLDPRT]
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2017-06-02 Found the problem in the DATCOM model! (kinda)
    It's something to do with the station-wise definition of the body not
    working at high Mach numbers. DATCOM gives normal outputs for the model
    at low Mach numbers, but it poops out at high (~1.5) Mach numbers.
    It also doesn't seem to like the altitudes being specified in inches,
    which is annoying. I'm not sure if changing the dimensions into feet
    would help. It would be a pain to do though... I'm not sure if it would
    be worth it to write a script that just divides all the numbers by
    12, lol.
    I'm also not sure if it would help at all to reformulate the body
    definition into an ogive and a cylinder. The DATCOM manual is a little
    unclear on what ex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
2017-06-12 further tweaking to R notebook and DATCOM model
    At first glance, the drag coefficients from OpenRocket and DATCOM seem
    to wildly disagree...
    OH MY GOD
    EVERYTHING IS TERRIBLE
    WHY AM I SPENDING MY TIME THIS WAY
    THIS IS SO TEDIOUS
    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
    [testPoints_DATCOM.csv, testPoints_OpenRocket.csv]
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2017-06-14 Uploaded the DXF files of the spacer walls used for laser cutting
    [CradleAssem.SLDASM, SpacerRib.DXF, SpacerRib.SLDPRT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]
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2017-10-28 added a hole-steady for the male ring
    Also fixed some dimensions on the female hole-steady.
    [fullJig.SLDASM, holeSteadyFemale.SLDPRT, holeSteadyMale.SLDPRT]
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2017-10-28 refinements to clamping tolerances
    [holeSteadyFemale.SLDPRT, holeSteadySpider.SLDPRT, holeSteadySpider_lower.SLDPRT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]
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2017-11-01 skookumized the cradle structure
    (should no longer experience a failure to chooch)
    [CradleAssem.SLDASM, CradleRibEnds.SLDPRT, CradleRibMid.SLDPRT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]
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2017-12-13 FIXED: thrust flange was flipped the wrong way
    [finCan.SLDASM]
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2018-02-13 up-to-date sims using the old (short) 98 mm case
    This includes:
    - OpenRocket output for an N2501 motor in the short case
    - OR output for an O3400 motor in a case we don't have
    - start of a notebook that tries to summarize OR output in a way that a
    noobie could start to get an idea of whether or not a launch
    configuration is safe
    - update (and renaming) of the OR model with the N motor
    [LV3_L13_N2501_2018-02-06.csv, LV3_L13_O3400_2018-02-06.csv]
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2018-03-23 redesigned cubesat cradle
    The side walls were brought in and given streamwise ribs.
    The telemetrum mount was given a cutout for the terminal block.
    The rings were replaced with bulkheads.
    [4-40x0.25standoff_93505A430_ALUM MALE-FEM THRDED HEX STANDOFF.SLDPRT, CradleRibMid.SLDPRT, CradleSideWalls.SLDPRT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]
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2018-03-23 fixed cosmetics
    [LV3.STL, Module18.SLDASM, carbonSleeve18.SLDPRT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]
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2018-04-26 set up for hand-calculation of bolt failure
    [No10-24x2_panHead_brass_94070A255_BRASS PAN HEAD PHILLIPS MACHINE SCREW.SLDPRT, No10-24x2buttonHead_316_98164A458_TYPE 316 SS BUTTON-HEAD SOCKET CAP SCREW.SLDP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]
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2018-04-30 fixed helicoil length
    [buttonRing.SLDPRT, hardPoint_mid.SLDASM]
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2018-04-30 correct length of fastener for buttons
    [No10-24x1.75_buttonHead_hex_91255A311_ALLOY STEEL BUTTON-HEAD SOCKET CAP SCREW.SLDPRT, No10-24x1.75_buttonHex_91255A311_ALLOY STEEL BUTTON-HEAD SOCKET CAP SCRE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]
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2018-05-13 cherry-picked old version of the thrust flange
    This is the version that doesn't have a hard point. We're just using the
    same hard point ring as the upper button.
    [motorMount.SLDPRT]
2018-05-15 FDM-able tip safety; missing dimension on ballast
    [ballastPlate.SLDDRW, tipSafety_3D.SLDPRT]
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

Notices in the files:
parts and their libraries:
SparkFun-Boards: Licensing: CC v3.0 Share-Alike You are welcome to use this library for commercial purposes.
